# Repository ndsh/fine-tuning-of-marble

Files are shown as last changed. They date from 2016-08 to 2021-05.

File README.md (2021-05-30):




<p align="center">
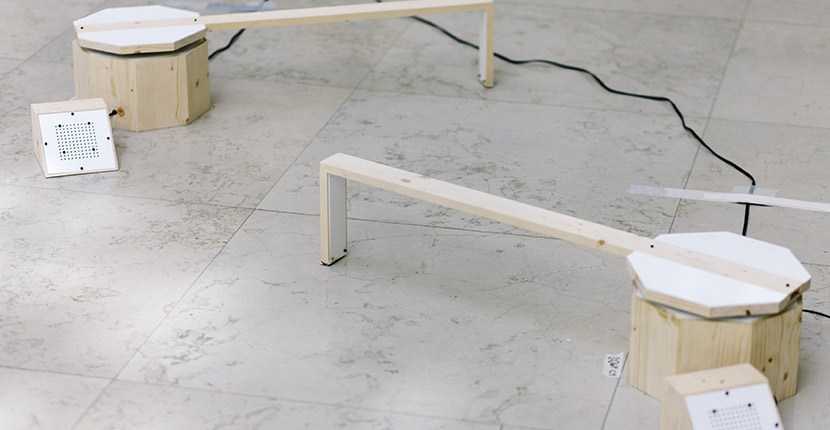
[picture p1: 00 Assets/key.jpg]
  
</p>

# floorScanners
Repository for the source code of an ongoing sound installation and performance. It was first presented at Resonate Festival in 2016 in its prototyped Version we called "Fine Tuning of Marble".

## Overview
* [Dependencies](#dependencies)
* [About](#about)
* [Classes](#classes)
* [PCB](#pcb)
* [Authors](#authors)

---

### About
tbd

---

### Dependencies
* [AccelStepper Library, v1.51](http://www.airspayce.com/mikem/arduino/AccelStepper/)
* [Teensy MIDI, v3.2](https://www.pjrc.com/teensy/td_libs_MIDI.html)

---

### Classes

These are the primary classes of the floorScanners living inside the /src/ folder

| Classname | Description | No. of Methods | Current working state |
|---|---|---|---|
| StateMachine | Organize States of a floorScanner | 4/4 | Working |
| Clock | Synchronize Scanners with a pulse | N/A | Deprecated (?) |
| Motor | Control Stepper Motor / Acceleration et al | 11/11 | Working |
| Score | - | N/A | Deprecated (?) |
| SensorHead | Reading and storing sensordata on a circle | 4/7 | Working |
| Synth | Synth output over speakers. Adjust timber etc | N/A | Working |
| Communication | Communication between Scanners over MIDI | N/A | Not working yet |
| MacAddress | Returns a Teensy MacAddress | 2/2 | Working |

<br>

These are secondary classes from the [Automatic Orchestra Library](https://github.com/automatic-orchestra/ao_library) and live next to the primary classes in the /src/ folder.
They have been copied over from the latest release and are basically version frozen as of now

| Classname | Description | No. of Methods | Current working state |
|---|---|---|---|
| CFOSynthesizer | CheapFatOpen Synth parts to control the DAC | ? | Working |
| CFOMidi | Send/Receive MIDI on the Teensy | ? | Working |

---

### PCB
Revisions
- [ ] Redesign the PCB stack into a single square board
- [ ] DRV8825 M0, M1, M2 to Pins
- [ ] Integrate TDA2030 circuit
- [ ] Switch terminal blocks with WAGO 2060 SMD
- [ ] Integrate PROTOSEQ circuit
- [ ] Expose all available pins
- [ ] Re-examine the audio interface between PROTOSEQ and TDA2030 (Is it really necessary to have the TDA2030?)

---

#### Authors
<sub>

Copyright (c) 2016 – 2021 (The Fine Tuning of Marble / floorScanners)
- &nearr; [Irena Kukric](https://www.irenakukric.com)
- &nearr; [Luiz Zanotello](https://www.luizzanotello.com)
- &nearr; [Julian Hespenheide](https://www.julian-h.de)

</sub>

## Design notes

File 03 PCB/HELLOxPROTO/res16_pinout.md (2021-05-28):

### res16 pinout

---

| PIN ID | TEENSY PIN |
| --- | --- |
| LED | |
| Photoresistor | |
| 1A | |
| 1B | |
| 2A | |

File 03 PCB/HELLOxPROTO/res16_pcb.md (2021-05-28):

## res16 pcb

---

### protoseq

* height: 75.18mm
* width: 76.96mm

218px height = 75.18 

new proto area pcb

* height: 75.18mm
* width: 76.96mm

---

### components

* TDA2030A module (2 pins to Teensy)
* Speaker
* LDR (exp-tech)
* LED
* SY42TH Stepper (exp-tech / flikto) + 2 from julian
* DRV8825 (exp-tech)
* Voltage Regulators? how? what? 12v sound, 24v stepper, 5v teensy

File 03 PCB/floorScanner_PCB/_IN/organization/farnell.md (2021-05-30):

**Farnell**

| PART | NAME | COMPONENT NR | QUANTITY | LINK |
| --- | --- | --- | --- | ---|
| R1 | Thumbwheel 10k* | 91AR50KLF | 1 | [1] |
| AUDIO/MIDI I/O | Connector Mini Jack | 502-35RAPC4BH3 | 3 | [2] |
| SW57 | SPDT Switch | 612-EG1218 | 1 | [3] |
| IC2 | MCP6002 | 579-MCP6002-I/P | 1 | [4] |

generic stuff we can always get from conrad/reichelt/my favorite ebay shops, since it's kind of a hassle to find and pick this stuff from farnell.
R2, R3, R4, C1, C2, headers and sockets = generic

taken from [jakob's bom].

*even tho jakob mentions it as a 10k thumbwheel, it's a 50k*

[jakob's bom]: https://docs.google.com/spreadsheets/d/1vRp1oA8k6EMiFsqzVwAAheo1oxb5zIVhr4JmbBJkZJc/edit#gid=1324172744
[1]: http://de.farnell.com/bourns/3352e-1-503lf/trimmer-potentiometer-50kohm-1turn/dp/1543806
[2]: http://de.farnell.com/switchcraft/35rapc4bh3/stecker-phono/dp/1608406?ost=502-35RAPC4BH3
[3]: http://de.farnell.com/e-switch/eg1218/slide-switch-spdt-200ma/dp/1905334?ost=612-EG1218
[4]: http://de.farnell.com/microchip/mcp6002-i-p/op-verst-rker-1-8v-imhz-dual-pdip8/dp/1292245

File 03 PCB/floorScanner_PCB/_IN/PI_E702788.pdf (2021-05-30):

### E702788 PCB view TOP (topview)

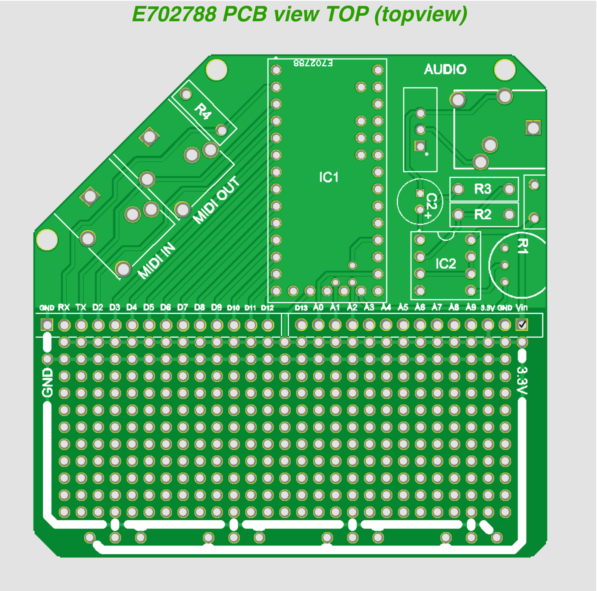
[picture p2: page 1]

E702788 TOP layer Image (topview)

E702788 BOTTOM layer Image (topview)

E702788 PCB view BOTTOM (bottomview)

# E702788 PCB Mechanical view (topview)

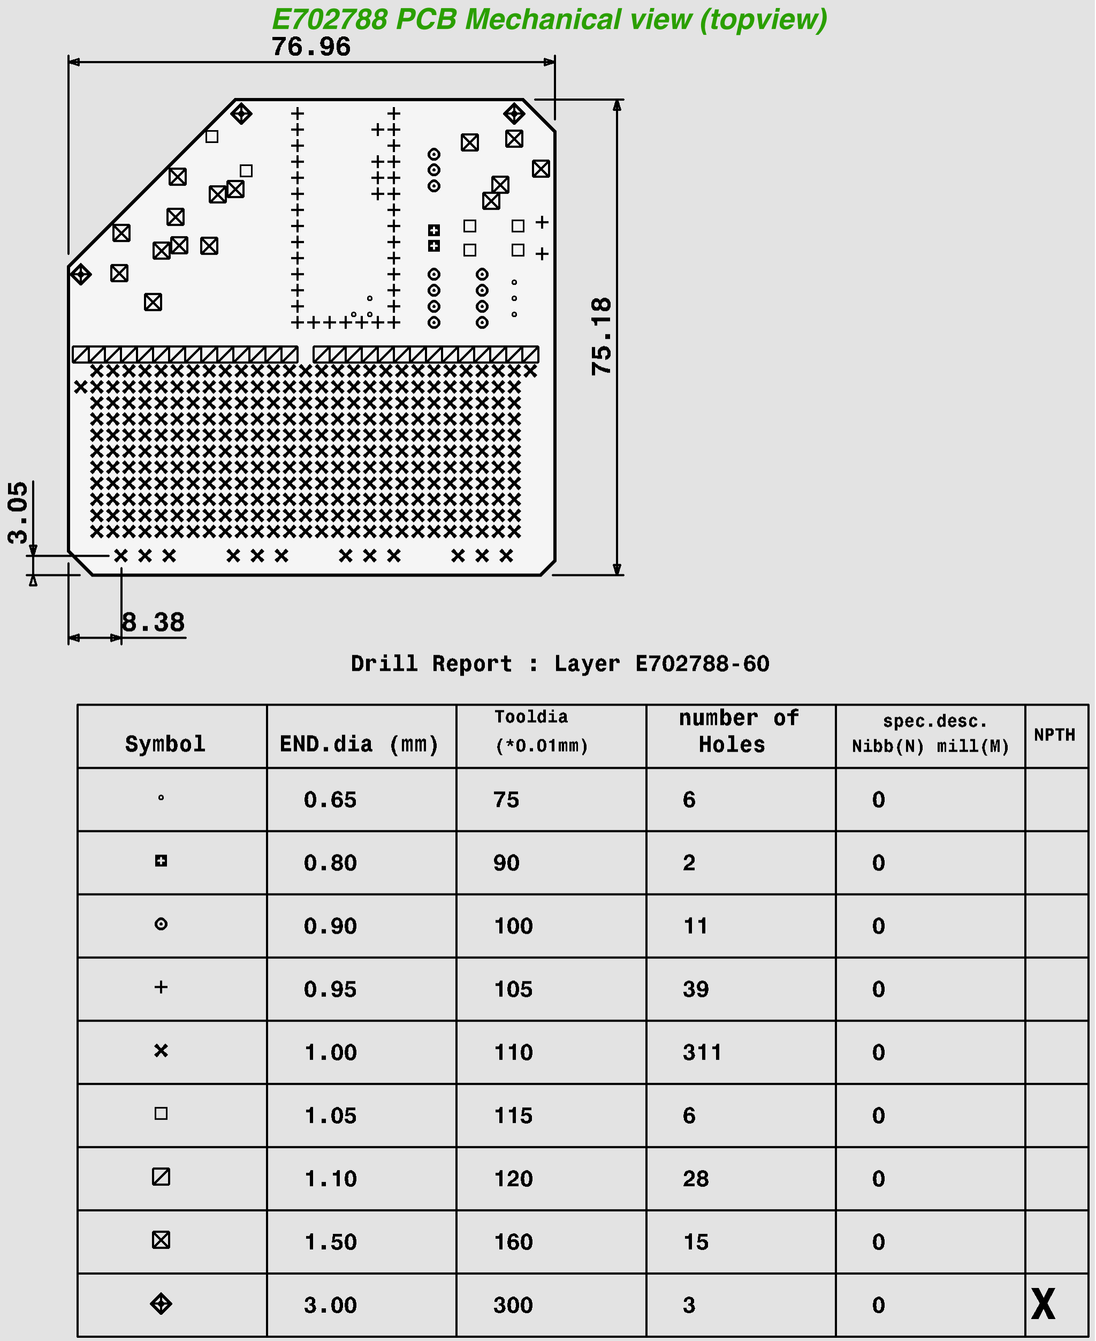
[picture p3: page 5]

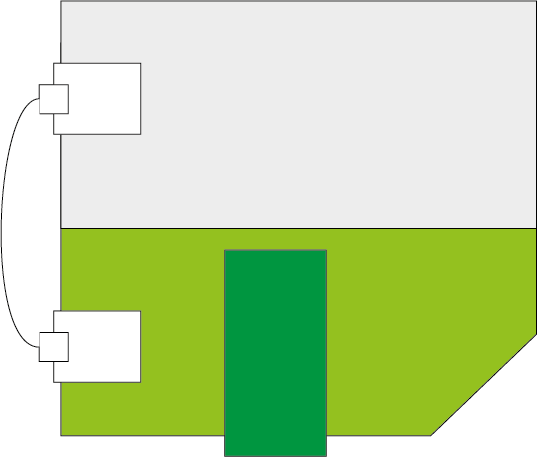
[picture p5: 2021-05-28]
03 PCB/HELLOxPROTO/proto-pcb.png

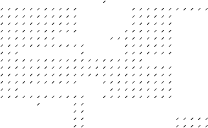
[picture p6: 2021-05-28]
03 PCB/HELLOxPROTO/overlay.png

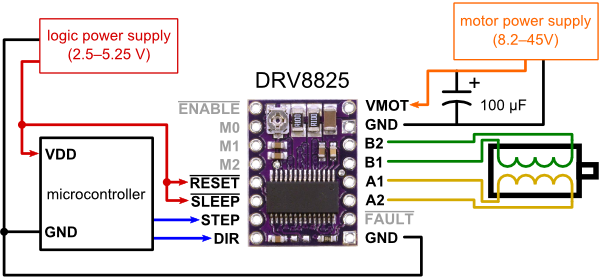
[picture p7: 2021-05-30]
03 PCB/floorScanner_PCB/_IN/drv8825_pins.png

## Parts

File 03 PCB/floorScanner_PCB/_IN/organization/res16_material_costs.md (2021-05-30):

# resonate16 components

| NAME | PRICE  | QUANTITY | SUM |
| --- | --- | --- | --- |
| TDA2030A | 4.16€  | 7 | 30€ |
| Fritzing PCBs | 16€ | 10 (batch) | 160€ |
| Speaker Chassis | 10€(?) | 7 | 70€ |
| LEDs | | | 5€ |
| Photoresistors | | | 5€ |
| Motors | 20€ | 7 | 140€ |
| Motor driver 8825  | 5€ | 7 | 35€ |
| Protosec | 60€ | 7 | 420€ |
| Power supplys | 20€ | 7 | 140€ |
| Cables for modules | 20€ | 7 | 140€ |
| Extension cables | 20€ | 7 | 140€ |
| Wood / Plexi | 25€ | 7 | 175€ |
| Paint | 30€ | 1 | 30€ |
| Copper plates | 20€ | 7 | 140€ |
| Ball bearings | 12€ | 4 | 48€ |
| Wheels | 10€ | 7 | 70€ |
| Screws and others  | 20€ | 7 | 140€ |
| Shipping costs | 50€ | 1 | 50€ |
| -----------------  | ------ | ---------- | ------------------------- |
| SUM | | | €1938,00 |
| FAT | | | *1.3 |
| -----------------  | ------ | ---------- | ------------------------- |
| TOTAL | | | €2500 |

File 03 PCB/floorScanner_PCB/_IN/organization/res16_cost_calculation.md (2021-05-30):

# resonate16 cost calculation

| NAME | PRICE  | QUANTITY | SUM | VIA |
| --- | --- | --- | --- | --- |
| Voltage Regulators | 3.10€  | 1 | 3,10€ | LUIZ |
| Ball Bearings | 27€ | 1 | 27€ | LUIZ |
| DRV8825 | 7,05€  | 8 | 56,47€ | LUIZ |
| Stepper (EXP-Tech) | 15,42€ | 2 | 30,84€ | LUIZ |
| Photoresistors | 1,26€  | 8 | 10,08€ | LUIZ |
| SMD Heatsink | 6,59€  | 1 | 6,59€ | LUIZ |
| Stepper | 19,55€ | 4 | 82,15€ | LUIZ |
| Teensies | 22,95€ | 10 | 229,50€ | DENNIS |
| PROTOSEQ REICHELT  | 41,09€ | 1 | 41,09€ | DENNIS |
| PROTOSEQ DIGIKEY | 20,96€ | 1 | 20,96€ | DENNIS |
| WOOD | 100€ | 1 | 100€ | DAVID |
| | | | | |
| | | | | |
| | | | | |
| | | | | |
| | | | | |
| | | | | |
| | | | | |
| -----------------  | ------ | ---------- | ------------------------- | |
| SUM | | | 507,78€ | |
| FAT | | | | |
| -----------------  | ------ | ---------- | ------------------------- | ------------------------- |
| LEFT | | | 1992,22€ | |

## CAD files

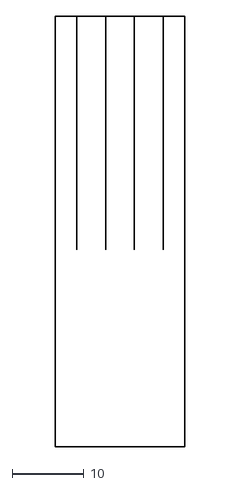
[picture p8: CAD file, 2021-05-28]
03 PCB/sensorHead/pcbShapeGrid.dxf
18.0 x 60.0

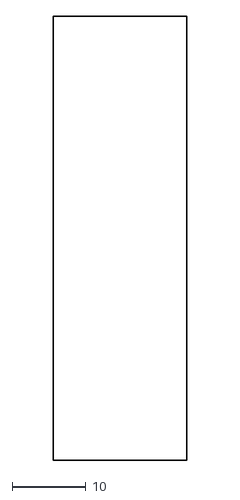
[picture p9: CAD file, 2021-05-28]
03 PCB/sensorHead/pcbShape.dxf
18.0 x 60.0

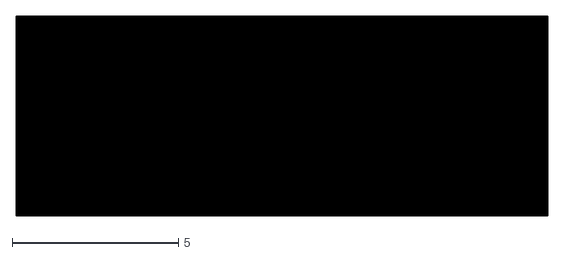
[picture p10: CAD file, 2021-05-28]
03 PCB/sensorHead/pcbShapeSilk.dxf
16.0 x 6.00

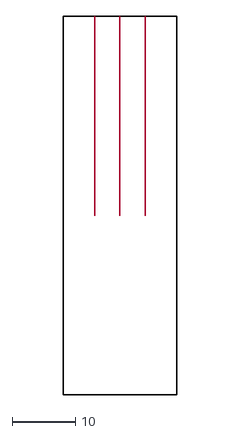
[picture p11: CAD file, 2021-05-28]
03 PCB/sensorHead/pcbShape_3grid.dxf
18.0 x 60.0

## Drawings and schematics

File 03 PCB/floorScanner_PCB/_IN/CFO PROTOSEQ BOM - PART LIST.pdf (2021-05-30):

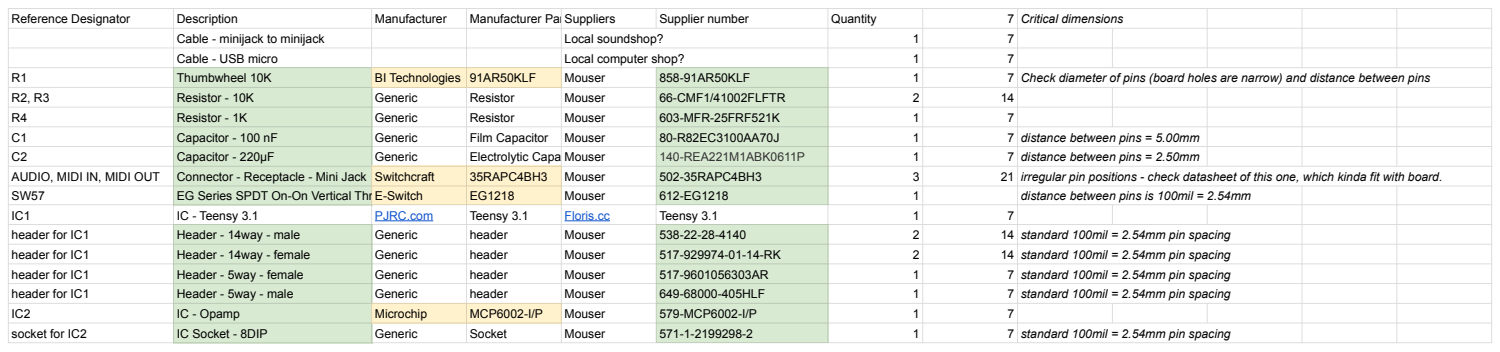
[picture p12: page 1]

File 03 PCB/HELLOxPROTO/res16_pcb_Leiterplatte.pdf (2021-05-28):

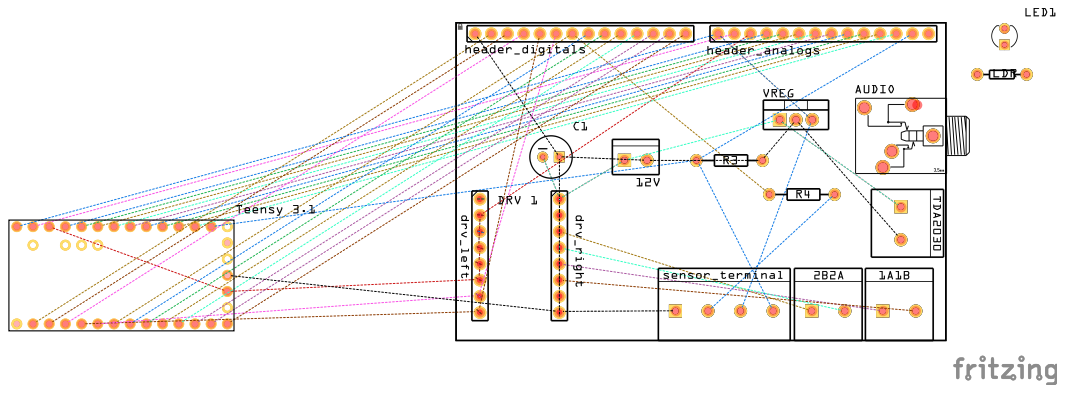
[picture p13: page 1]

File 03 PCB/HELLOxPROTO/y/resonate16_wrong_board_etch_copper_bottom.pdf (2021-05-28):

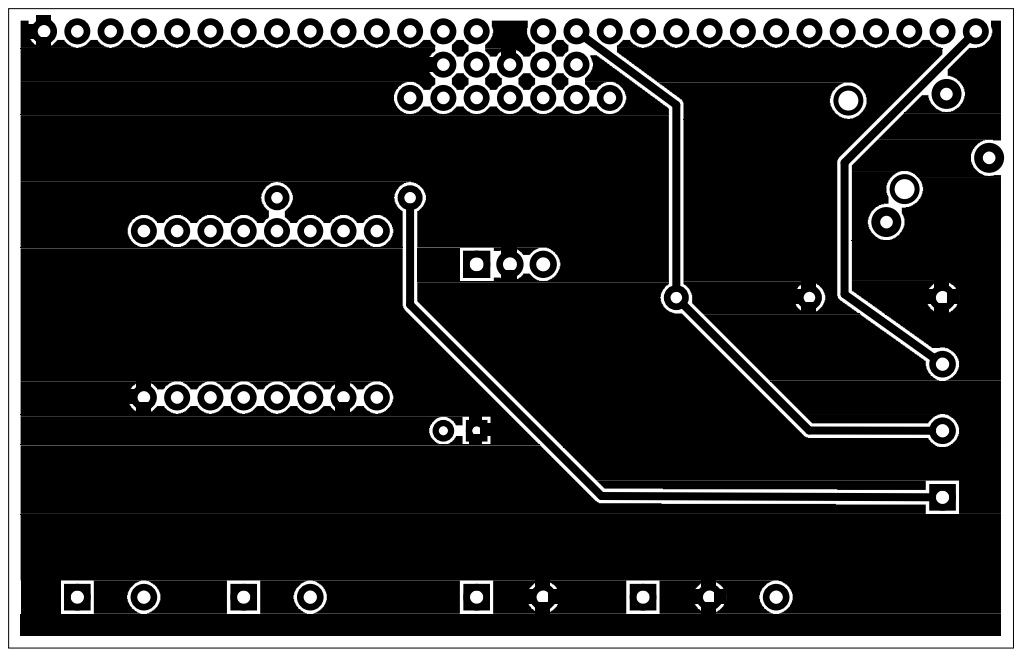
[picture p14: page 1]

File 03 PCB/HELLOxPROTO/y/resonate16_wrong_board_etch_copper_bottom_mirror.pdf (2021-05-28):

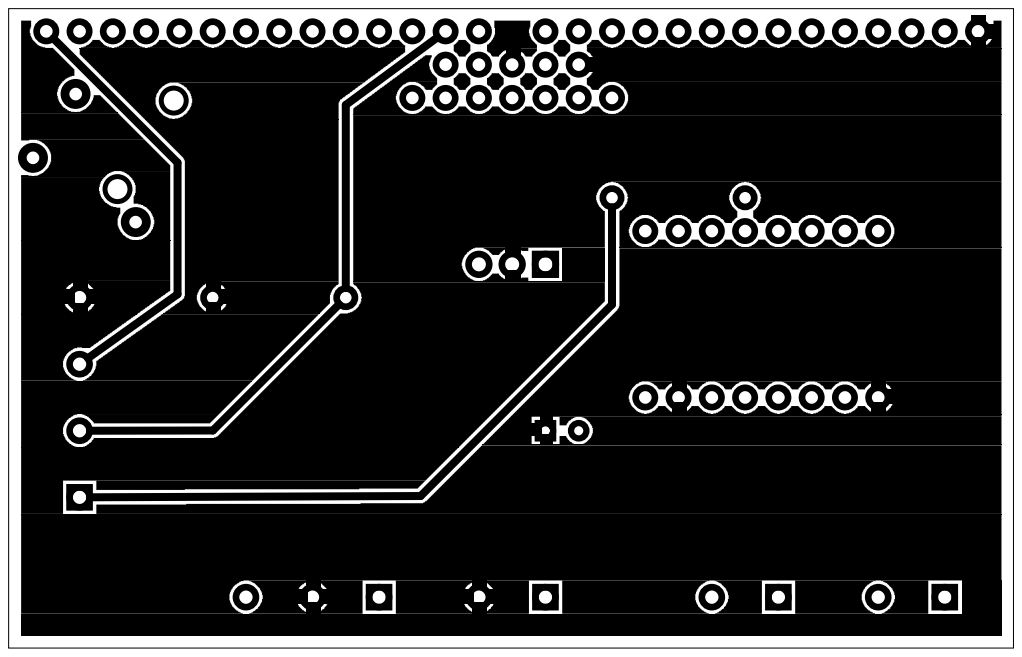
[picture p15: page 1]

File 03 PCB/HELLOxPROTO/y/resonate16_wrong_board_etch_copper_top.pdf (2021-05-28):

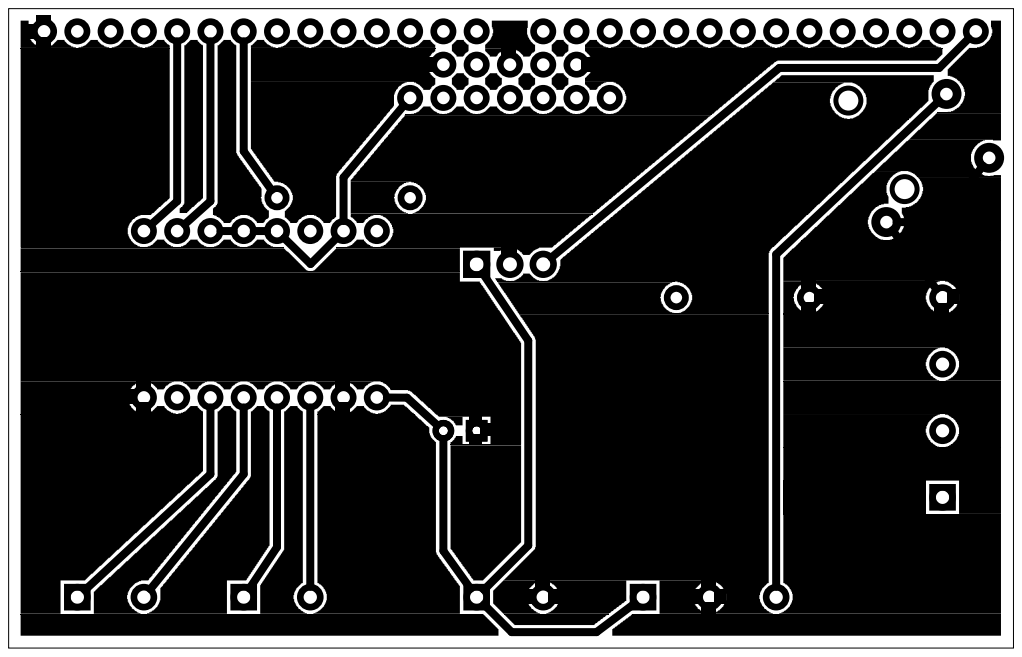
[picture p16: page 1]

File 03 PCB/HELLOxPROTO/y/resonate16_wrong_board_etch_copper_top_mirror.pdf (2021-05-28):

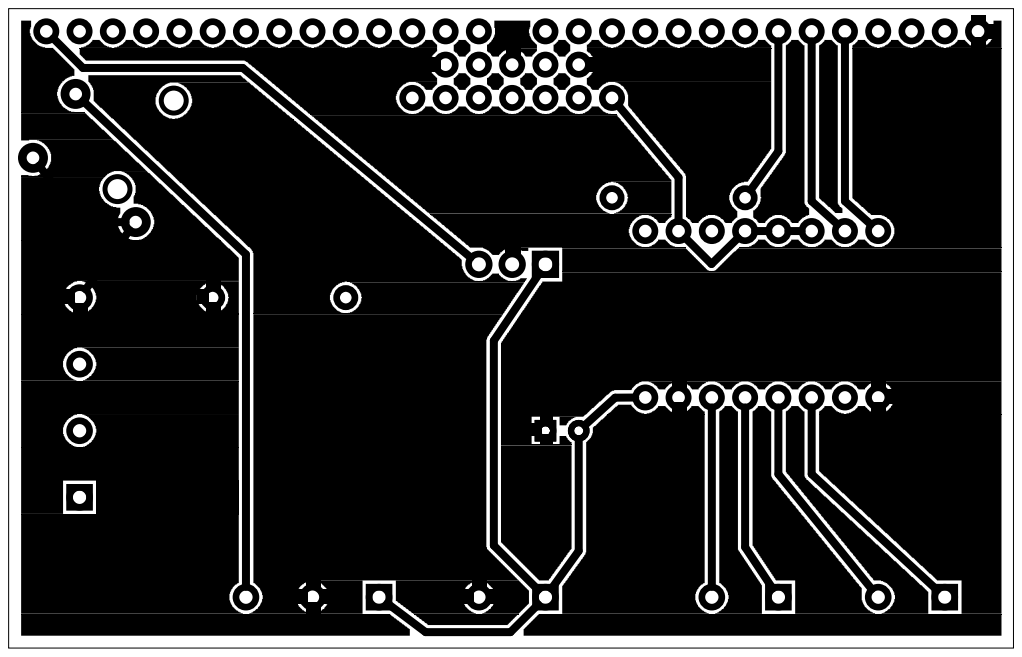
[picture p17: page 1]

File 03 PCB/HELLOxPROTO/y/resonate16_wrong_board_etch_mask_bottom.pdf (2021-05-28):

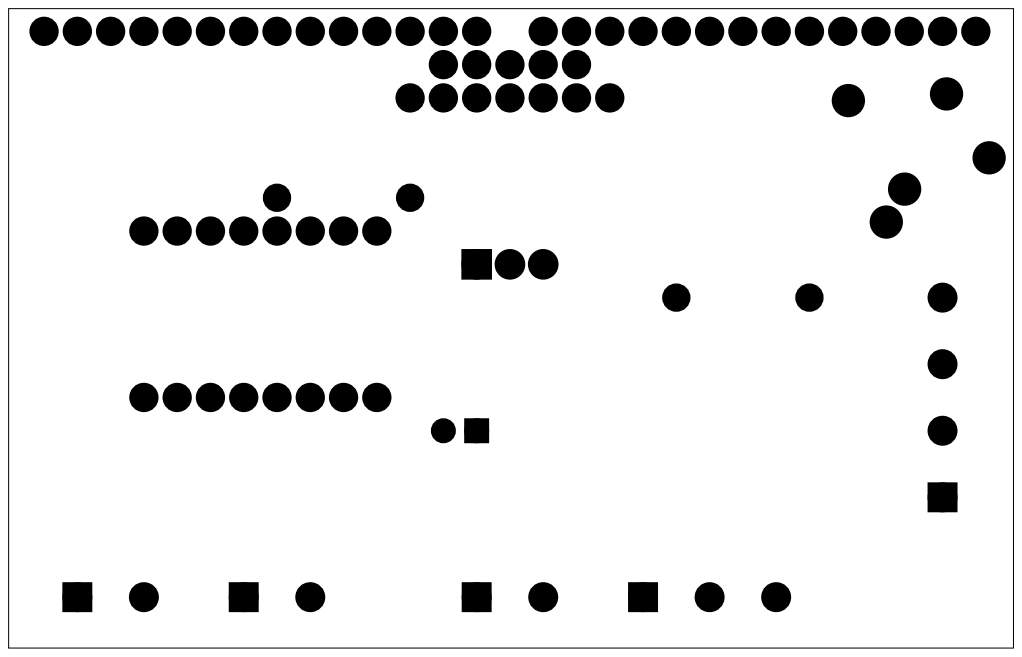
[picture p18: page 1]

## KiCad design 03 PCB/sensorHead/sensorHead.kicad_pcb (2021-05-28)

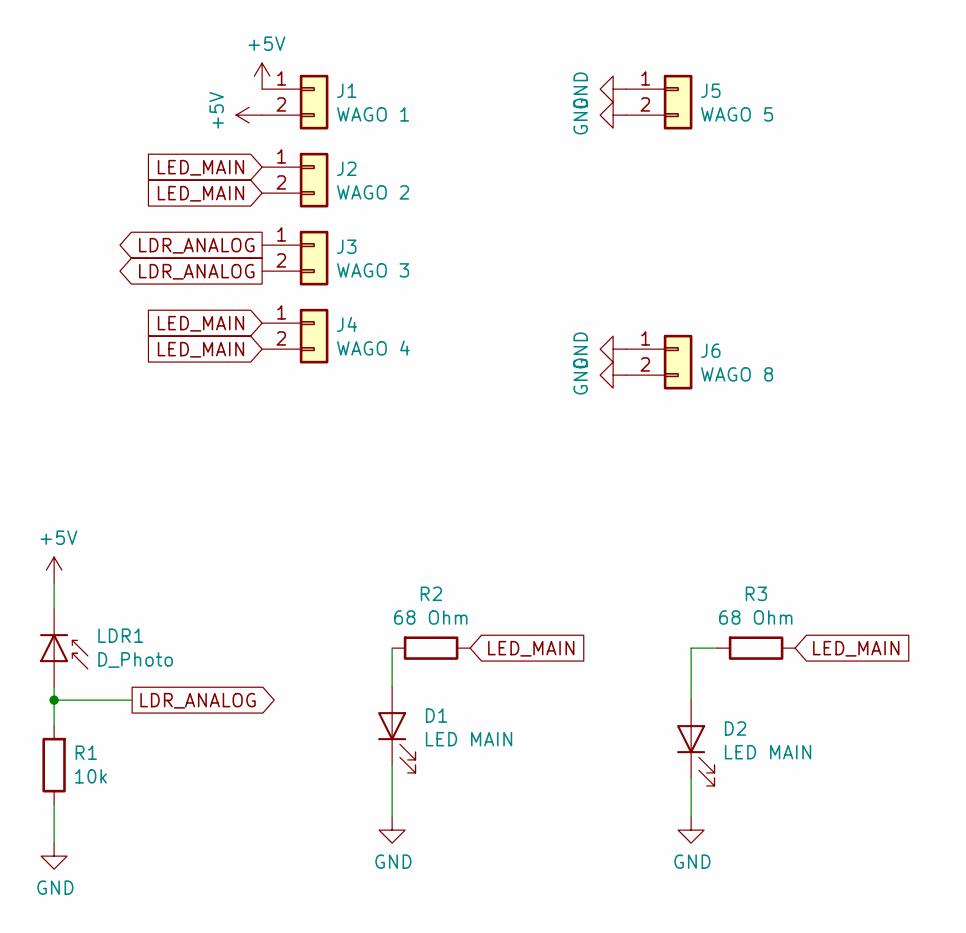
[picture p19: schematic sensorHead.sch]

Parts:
D1: LED MAIN; LED_1206_3216Metric_Pad1.42x1.75mm_HandSolder
D2: LED MAIN; LED_0805_2012Metric_Pad1.15x1.40mm_HandSolder
J1: WAGO 1; WAGOSMD_p_2060_451_aktualisiert
J2: WAGO 2; WAGOSMD_p_2060_451_aktualisiert
J3: WAGO 3; WAGOSMD_p_2060_451_aktualisiert
J4: WAGO 4; WAGOSMD_p_2060_451_aktualisiert
J5: WAGO 5; WAGOSMD_p_2060_451_aktualisiert
J6: WAGO 8; WAGOSMD_p_2060_451_aktualisiert
LDR1: D_Photo; R_LDR_5.2x5.2mm_P3.5mm_Horizontal
R1: 10k; R_0805_2012Metric_Pad1.15x1.40mm_HandSolder
R2, R3: 68 Ohm; R_0805_2012Metric_Pad1.15x1.40mm_HandSolder

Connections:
+5V: J1.1, J1.2, LDR1.1 (K)
GND: D1.1 (K), D2.1 (K), J5.1, J5.2, J6.1, J6.2, R1.1
LDR_ANALOG: J3.1, J3.2, LDR1.2 (A), R1.2
LED_MAIN: J2.1, J2.2, J4.1, J4.2, R2.1, R3.1
unnamed: D1.2 (A), R2.2
unnamed: D2.2 (A), R3.2

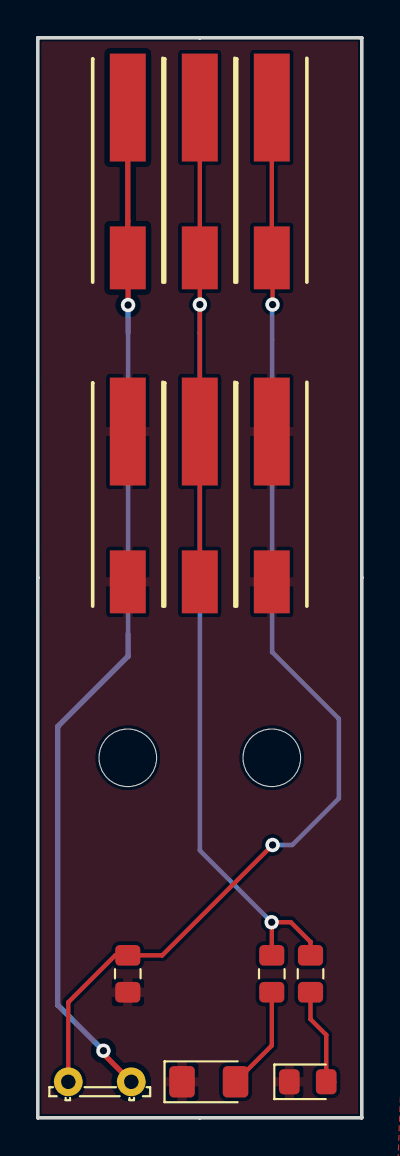
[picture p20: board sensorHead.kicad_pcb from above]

Board: 2 copper layers, 18.0 x 60.0 mm, 12 parts (0 on the bottom side), 6 nets.

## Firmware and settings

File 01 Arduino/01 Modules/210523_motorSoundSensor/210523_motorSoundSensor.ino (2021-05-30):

/*
 * You can try putting a capacitor in parallel with the 2K resistor. For example, the RC time constant (R x C) of 2K and 500uF is one second. (The effective "R" is actually the parallel equivalent of the fixed resistor and LDR, so the actual time constant will be less.)

Or you can try some [u]smoothing[/u].

And, I assume the whole thing is in a light-tight box? Fluorescent lights flicker at the power line frequency.

*/
#include <spi4teensy3.h>
#include <EEPROM.h>
#include <CFO_BODYSEQ.h>
#include <AccelStepper.h>

boolean noteIsOn = false;
int n = 0;
int dir = 1;
int rootNote = 36;
int note[] = {0,12,3,19,15,9,5,24,7};

long time = 0;
long lastTime = 0;
long timeDelay = 60;

#define MOTOR_DIR_PIN 3
#define MOTOR_STEP_PIN 4
#define SENSOR_PIN A0
#define LED_PIN 5

//AccelStepper stepper; // Defaults to AccelStepper::FULL4WIRE (4 pins) on 2, 3, 4, 5
AccelStepper stepper(AccelStepper::FULL2WIRE, 4, 3);

int counter = 0;

void setup() {
  //stepper = AccelStepper::FULL2WIRE, MOTOR_STEP_PIN, MOTOR_DIR_PIN;
  Music.init();
  Music.setWaveform(SINE);
  //Music.setDetune(1.005); 
  /*
  Music.enableEnvelope1();
  Music.setEnv1Attack(2);
  Music.setEnv1Decay(4);
  Music.setEnv1Sustain(20);
  Music.setEnv1Release(30);
  */

  pinMode(SENSOR_PIN, INPUT);
  pinMode(LED_PIN, OUTPUT);
  digitalWrite(LED_PIN, HIGH);

  stepper.setMaxSpeed(1000);
  stepper.setSpeed(100);  
}

void loop() {
  
  int val = analogRead(SENSOR_PIN);
  //val = random(0, 1023);
 
  
  int mapped = map(val, 0, 1023, 20, 64);
  Serial.println(mapped);
  if(val > 0) Music.noteOn(rootNote+mapped);
  //stepper.move(1);
  stepper.runSpeed();
  //stepper.runToPosition();
  delay(10);
  /*
  time = millis();
  if(time - lastTime > timeDelay) {
    if(!noteIsOn) {
      Music.noteOn(rootNote+note[n]);
      noteIsOn = true;
      n = n + dir;
      if(n > 7)
      {
        dir = -1;
      }
      else if(n < 1)
      {
        dir = 1;
      }
    } else {
      Music.noteOff();
      noteIsOn = false;
    }
    lastTime = time;
  }
  */
}

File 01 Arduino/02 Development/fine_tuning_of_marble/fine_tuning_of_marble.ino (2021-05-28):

/*

    ./~     FineTuningOfMarble.ino  
    ./~     Copyright (c) 2016 The Fine Tuning of Marble

    ./~     [!] https://github.com/ndsh/fine-tuning-of-marble
    
    . . . . . . . . . . . . . . . . . . . . . . . . . . . . . . . . . . . . . . . . .
    ~ ~ ~ ~ ~ ~ ~ ~ ~ ~ ~ ~ ~ ~ ~ ~ ~ ~ ~ ~ ~ ~ ~ ~ ~ ~ ~ ~ ~ ~ ~ ~ ~ ~ ~ ~ ~ ~ ~ ~ ~ 

*/

//Definitions

#define SCORE 0 //Score in play
#define FULLREV 230400 //9:1 25600
#define PULSE_INTERVAL 50 //In milliseconds
#define TOTALPODS 7 //Total number of PODs in play
#define DEBUG true

#define SENSOR_PIN A0
#define MOTOR_DIR_PIN 3
#define MOTOR_STEP_PIN 4
#define LED_PIN 5
#define START_PIN 6
#define ONBOARD_LED_PIN 13

//Main Include
#include "src/FTPod.h"

//Instances
FTPod* Pod;

/* +++++++++++++++++++++++++++++++++++++++++++++++++++++++++++++++++++++++++++++++ */

void setup() {
  //Setup Pins
  pinMode(SENSOR_PIN, INPUT); 
  pinMode(LED_PIN, OUTPUT);
  pinMode(MOTOR_DIR_PIN, OUTPUT);
  pinMode(MOTOR_STEP_PIN, OUTPUT);
  pinMode(START_PIN, INPUT_PULLDOWN);
  pinMode(ONBOARD_LED_PIN, OUTPUT);
  delay(1000);

#if DEBUG
  Serial.begin(57600);
  Serial.println("~FTApp: INIT");
  Serial.println();
#endif

  //Create Pod
  Pod = new FTPod(SENSOR_PIN, LED_PIN, MOTOR_DIR_PIN, MOTOR_STEP_PIN, START_PIN, ONBOARD_LED_PIN, FULLREV, TOTALPODS, SCORE, PULSE_INTERVAL);
}

void loop() {
  //Update Pod
  Pod->update();
}

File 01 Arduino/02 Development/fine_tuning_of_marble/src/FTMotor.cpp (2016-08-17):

/*

    ./~     FTMotor.cpp
    ./~     Copyright (c) 2016 The Fine Tuning of Marble
	

    . . . . . . . . . . . . . . . . . . . . . . . . . . . . . . . . . . . . . . . . .
    ~ ~ ~ ~ ~ ~ ~ ~ ~ ~ ~ ~ ~ ~ ~ ~ ~ ~ ~ ~ ~ ~ ~ ~ ~ ~ ~ ~ ~ ~ ~ ~ ~ ~ ~ ~ ~ ~ ~ ~ ~ 
    
*/

#include "FTMotor.h"

FTMotor::FTMotor(int stepPin, int dirPin, long fullRevolution)
{
	//Configure stepper
	mStepper = new AccelStepper(AccelStepper::FULL2WIRE, stepPin, dirPin);
	mStepper->setMaxSpeed(MAXSPEED);
	mStepper->setSpeed(0);
	mStepper->setCurrentPosition(0);

	//Set initial states
	mSpeed = 0;
	mRangeIn = 0;
	mRangeOut = 0;
	mMaxSpeedFactor = 1;
	mIsConstant = false;
	mCounter = 0;
  	fullRev = fullRevolution;
}

void FTMotor::update() {
	//Update speed
	if (!mIsConstant) updateSpeed();
	mStepper->setSpeed(mSpeed);
	//Move motor
	mStepper->runSpeedToPosition();
}

/*+++++++++++++++++++++++++++++++++++++++++++++++++++++++++++++++++++++++++++++++++++
	Public
+++++++++++++++++++++++++++++++++++++++++++++++++++++++++++++++++++++++++++++++++++*/

void FTMotor::rotate(float rotations,int direction)
{
	//Rotate the motor to times * full revolution.
	//Direction = -1 counterclockwise, 1 clockwise
	mLastPos = mStepper->currentPosition();
	mTargetPos = mLastPos + (fullRev * rotations * direction);
	mTargetDistance = getAbsoluteDistance(mLastPos,mTargetPos);
	mStepper->moveTo(mTargetPos);

	#if DEBUG_MOTOR
		Serial.print("~FTMtr::rotate()-› ");
		Serial.print(rotations);
		Serial.print("times / direction: ");
		Serial.print(direction);
		Serial.print(" / mTargetPos: ");
		Serial.println(mTargetPos);
	#endif
}

void FTMotor::runTo(long absolutePos, int direction, int rotations)
{
	#if DEBUG_MOTOR
		Serial.print("~FTMtr::runTo()-› absolutePos: ");
		Serial.print(absolutePos);
		Serial.print(" direction: ");
		Serial.print(direction);
		Serial.print(" rotations: ");
		Serial.println(rotations);
	#endif

	//Direction = -1 counterclockwise, 0 the closest, 1 clockwise
	mLastPos = mStepper->currentPosition();
	mTargetPos = getNewTargetRelativePosition(absolutePos,direction,rotations);
	mTargetDistance = getAbsoluteDistance(mLastPos,mTargetPos);
	mStepper->moveTo(mTargetPos);
}

void FTMotor::stop()
{
	mLastPos = mStepper->currentPosition();
	mIsConstant = true;
	mSpeed = 0;
	#if DEBUG_MOTOR
		Serial.println("~FTMtr::stop()");
	#endif
}

void FTMotor::setConstantSpeed(float speedFactor)
{
	//Linear constant speed of speedFactor (0 to 1) * MAXSPEED
	mIsConstant = true;
	mSpeed = MAXSPEED * speedFactor;
	#if DEBUG_MOTOR
		Serial.print("~FTMtr::setConstantSpeed()-› ");
		Serial.println(mSpeed);
	#endif
}

void FTMotor::setAccelSpeed(float in, float out, float maxSpeedLimiter)
{
	//in (0 to 1), define length of ease in curve
	//out (0 to 1), define length of ease out curve
	//speedFactor (0 to 1) limits the MAXSPEED (height) of the motion curve
	mIsConstant = false;
	mRangeIn = in;
	mRangeOut = out;
	mMaxSpeedFactor = maxSpeedLimiter;
	#if DEBUG_MOTOR
		Serial.print("~FTMtr::setAccelSpeed()-› in: ");
		Serial.print(in);
		Serial.print(" out: ");
		Serial.print(out);
		Serial.print(" maxSpeedLimiter: ");
		Serial.println(maxSpeedLimiter);
	#endif
}

bool FTMotor::isMoving()
{
	if (mStepper->distanceToGo() == 0)
	{
		return false;
	}
	else
	{
		return true;
	}
}

long FTMotor::getCurrentAbsolutePosition()
{
	//Calculates an absolute position (0 to fullRev) relative to the current relative one

	//Main calculation
	long currentRelativePos = mStepper->currentPosition();
	int currentRevolutions;
	long absolutePos;
	if (currentRelativePos < 0)
	{
		currentRevolutions = abs(floor(currentRelativePos / fullRev));
		absolutePos = currentRelativePos + (fullRev * currentRevolutions);
	}
	else
	{
		currentRevolutions = currentRelativePos / fullRev;
		absolutePos = currentRelativePos - (fullRev * currentRevolutions);
	}

	//Correction of range (from -fullRev to fullRev, to 0 to fullRev)
	if (absolutePos < 0)
	{
		absolutePos += fullRev;
	}

	#if DEBUG_MOTOR
		Serial.print("~FTMtr::getCurrentAbsolutePosition()-› currentRelativePos: ");
		Serial.print(currentRelativePos);
		Serial.print(" currentRevolutions: ");
		Serial.print(currentRevolutions);
		Serial.print(" currentAbsolutePos: ");
		Serial.println(absolutePos);
	#endif

	return absolutePos;
}

long FTMotor::getCurrentRelativePosition()
{
	long relativePos = mStepper->currentPosition();
	#if DEBUG_MOTOR
		Serial.print("~FTMtr::getCurrentRelativePosition()-› ");
		Serial.println(relativePos);
	#endif
	return relativePos;
}

int FTMotor::getTotalMovements()
{
	#if DEBUG_MOTOR
		Serial.print("~FTMtr::getNumberOfMovements()-› ");
		Serial.println(mCounter);
	#endif
	return mCounter;
}

void FTMotor::updateCounter()
{
	mCounter++;
	#if DEBUG_MOTOR
		Serial.print("~FTMtr::updateCounter()-› ");
		Serial.println(mCounter);
	#endif
}

/*+++++++++++++++++++++++++++++++++++++++++++++++++++++++++++++++++++++++++++++++++++
	Private
+++++++++++++++++++++++++++++++++++++++++++++++++++++++++++++++++++++++++++++++++++*/

long FTMotor::getNewTargetRelativePosition(long newAbsolutePos, int direction, int rotations)
{
	//Calculates a relative position relative to an absolute one (0 to fullRev)
	//Does further recquired calculations regarding extra locked direction or rotation

	long newRelativePos = mStepper->currentPosition();
	long currentAbsolutePos = getCurrentAbsolutePosition();
	long distance = newAbsolutePos - currentAbsolutePos;

	switch(direction)
	{
		case -1:
			if (distance < 0)
			{
				//Already going to -1
				newRelativePos += distance - (fullRev*rotations);
			}
			else
			{
				//Force to -1
				newRelativePos += distance - (fullRev*(rotations+1));
			}
		break;

		case 0:
			if (distance < 0)
			{
				//Going -1
				newRelativePos += distance - (fullRev*rotations);
			}
			else
			{
				//Going 1
				newRelativePos += distance + (fullRev*rotations);
			}
		break;

		case 1:
			if (distance < 0)
			{
				//Force to 1
				newRelativePos += distance + (fullRev*(rotations+1));
			}
			else
			{
				//Already going to 1
				newRelativePos += distance + (fullRev*rotations);
			}
		break;
	}

	#if DEBUG_MOTOR
		Serial.print("~FTMtr::getNewTargetRelativePosition()-› ");
		Serial.print("newAbsolutePos: ");
		Serial.print(newAbsolutePos);
		Serial.print(" distance: ");
		Serial.print(distance);
		Serial.print(" newRelativePos: ");
		Serial.println(newRelativePos);
	#endif

	return newRelativePos;
}

long FTMotor::getAbsoluteDistance(long lastPos, long newPos)
{
	long distance;
	distance = newPos - lastPos;
	return distance;
}
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

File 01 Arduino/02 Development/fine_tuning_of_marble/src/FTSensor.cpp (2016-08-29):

/*

    ./~     FTSensor.cpp
    ./~     Copyright (c) 2016 The Fine Tuning of Marble


    . . . . . . . . . . . . . . . . . . . . . . . . . . . . . . . . . . . . . . . . .
    ~ ~ ~ ~ ~ ~ ~ ~ ~ ~ ~ ~ ~ ~ ~ ~ ~ ~ ~ ~ ~ ~ ~ ~ ~ ~ ~ ~ ~ ~ ~ ~ ~ ~ ~ ~ ~ ~ ~ ~ ~

*/

#include "FTSensor.h"

FTSensor::FTSensor(int sensorPin, int ledPin, long fullRevolution)
{
  mFullRev = fullRevolution;
	mStepRange = fullRevolution / MAXVALUES;
  mPinLED = ledPin;
  mPinSensor = sensorPin;
  mIsParsing = false;
  mParsingIndex = 0;
  mFilterIndex = 0;
  mCycleCounter = 0;
  mCurrentSensorValue = analogRead(mPinSensor);
}

/*+++++++++++++++++++++++++++++++++++++++++++++++++++++++++++++++++++++++++++++++++++
	Public
+++++++++++++++++++++++++++++++++++++++++++++++++++++++++++++++++++++++++++++++++++*/

void FTSensor::update(long absolutePos) {
  if (mCycleCounter < SENSOR_CYCLE)
  {
     mCycleCounter++;
  }
  else
  {
    mCycleCounter = 0;
    if (mIsParsing && mParsingIndex < MAXVALUES)
    {
      mCurrentSensorValue = filterData(analogRead(mPinSensor));
      parseDataToArray(absolutePos);
    }
    else
    {
      mCurrentSensorValue = getDataFromAbsolutePos(absolutePos);
    }
  }
}

void FTSensor::toggleLED(bool state)
{
	if (state)
	{
		digitalWrite(mPinLED, HIGH);
	}
	else
	{
		digitalWrite(mPinLED, LOW);
	}
}

void FTSensor::toggleDataParsing(bool state)
{
  mIsParsing = state;
}

/*+++++++++++++++++++++++++++++++++++++++++++++++++++++++++++++++++++++++++++++++++++
	Private
+++++++++++++++++++++++++++++++++++++++++++++++++++++++++++++++++++++++++++++++++++*/

  int FTSensor::filterData(int raw){

  //Assign to filter array
  mFilterDataArray[mFilterIndex] = raw;
  if (mFilterIndex < FILTERSAMPLES-1)
  {
    mFilterIndex++;
  }
  else
  {
    mFilterIndex = 0;
  }

  //Calculate average
  int sum = 0;
  for (int i = 0; i < FILTERSAMPLES; i++)
  {
    sum += mFilterDataArray[i];
  }

  int average = sum/FILTERSAMPLES;

  return average;
}

void FTSensor::parseDataToArray(long absolutePos)
{
  if (absolutePos > mStepRange * (mParsingIndex+1))
  {
    mParsingIndex++;
    #if DEBUG_SENSOR
      Serial.print("~FTSns::parseDataToArray()-› ");
      Serial.print("mParsingIndex: ");
      Serial.print(mParsingIndex);
      Serial.print(" absolutePos: ");
      Serial.print(absolutePos);
      Serial.print(" mCurrentSensorValue: ");
      Serial.println(mCurrentSensorValue);
    #endif
  }

  mPositionArray[mParsingIndex] = absolutePos;
  mDataArray[mParsingIndex] = mCurrentSensorValue;

}

int FTSensor::getDataFromAbsolutePos(long absolutePos)
{
  //Find the closest position using the Step Range as reference
  int idx = floor(absolutePos/mStepRange);

  /*
  //Find the real closest position
  long d = abs(mPositionArray[0] - absolutePos);
  int idx = 0;
  for(int c = 1; c < MAXVALUES; c++){
      long cd = abs(mPositionArray[c] - absolutePos);
      if(cd < d){
          idx = c;
          d = cd;
      }
  }
  */

  /*
  //Following debug lines are heavy on Teensy. Use it only when needed.
  #if DEBUG_SENSOR
    Serial.print("~FTSns::getDataFromAbsolutePos()-› ");
    Serial.print(absolutePos);
    Serial.print(" -> closestPosition: ");
    Serial.print(mPositionArray[idx]);
    Serial.print(" -> returning Data: ");
    Serial.println(mDataArray[idx]);
  #endif
  */
  return mDataArray[idx];
}

long FTSensor::getAbsolutePosFromData(int data)
{
  //Find the closest data point in the array and retrieve its position
  int d = abs(mDataArray[0] - data);
  int idx = 0;
  for(int c = 1; c < MAXVALUES; c++){
      int cd = abs(mDataArray[c] - data);
      if(cd < d){
          idx = c;
          d = cd;
      }
  }

  return mPositionArray[idx];
}

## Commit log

2016-06-03 FTSensor implementation + FTMotor development
    Implemented initial state for the FTSensor class. Updated FTMotor. Instantiated motor to start programming its movement functions.
2016-06-17 FTMotor update: speed functions & position control
    Finalized speeding functions. Finalized position conversion functions. Updated minor semantics of variables and functions. Still missing: bux fix of CCW runTo(), and callback functions.
    [FTMotor.cpp, FTPod.cpp, fine_tuning_of_marble.ino]
2016-07-08 FTMotor Improvements
    Fixed the bug on forcing negative rotations, debuged, improved, and tested all the functions for movement and speed control. Included an example of usage inside FTPod. Included DEBUG messages.
    [FTMotor.cpp, FTPod.cpp, fine_tuning_of_marble.ino]
2016-07-15 FTSensor Implementation + General updates
    Implemented the sensor parsing, and filtering basic functions (needs testing together with motor functions). Updated full revolution value. Updated DEBUG functions.
2016-07-22 FTMotor Update
    Included functions to get and convert the current absolute and relative positions of the motor.
2016-07-22 FTMotor Update
    Fixed a few bugs on negative forced direction, updated the getCurrentAbsolutePosition to return only from 0 to fullRev (instead of -fullRev to fullRev), and included/updated debug messages.
    [FTMotor.cpp]
2016-07-22 FTPod: macAddresses + Music
    - void retrieveMacAdress() gets the teensy's MAC and stores in a variable AKA setMacAdress()
    - String getMacAdresses() returns the MAC
    - on Constructor of FTPod a small jingle plays to ensure that the Synthesizer is enabled, alive and well running!
2016-07-29 added digital pin: PODZERO
    if left with no SPDT switch, it pulls low
2016-07-29 FTClock Implementation + FTPod Update
    Implemented FTClock pulse functions, and updated FTPod accordingly to update the clock. Also made minor semantic changes on the button pin.
2016-07-30 pinMode: START_PIN
    i think it should be pulled down instead of a floating pin. so we don't have to put any more redundant resistors on the pcbs
2016-08-09 Score Implementation + FTPod + FTClock + FTCom Upd
    Implemented the system for controlling the current act and composition in play. Deleted FTScore due to simplified structure to manipulate the acts. Updated FTPod, FTClock, FTCom and the main .ino wit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
2016-08-13 App+FTPod+FTCom: OnBoard LED for communication
2016-08-16 mishap in naming MIDI methods
    eg.
    sendControlChange = name of method
    controlChange = the actual string that can be received and processed via a switch-case
2016-08-29 FTScore + FTAct Update
    Current act id is now stored at FTPod, which communicates to the FTScore to get/update the states of each act. Also corrected semantic errors.
2021-05-28 add arduino
    old stable version from luiz
    new module tests for getting started in 2021
2021-05-28 it is all about the pcbs
    HELLOxPROTO PCB, 2016
    sensorHead, 2020
    [DRV 8825 Stepper Motor Carrier, High Current.fzz, pcbShape.dxf, pcbShapeGrid.dxf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]
2021-05-28 naming scheme of folders
    [DRV 8825 Stepper Motor Carrier, High Current.fzz, pcbShape.dxf, pcbShapeGrid.dxf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]
2021-05-28 removed PCB out
    [sensorHead-B_Cu.gbr, sensorHead-B_Mask.gbr, sensorHead-B_Paste.gbr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]
2021-05-28 rename of sensorHead folder
    [pcbShape.dxf, pcbShapeGrid.dxf, pcbShapeSilk.dxf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]
2021-05-28 removed some git update stream / stashed changes
    but code is still not runnable and probably won’t be for some time
    [FTCom.cpp, FTPod.cpp]
